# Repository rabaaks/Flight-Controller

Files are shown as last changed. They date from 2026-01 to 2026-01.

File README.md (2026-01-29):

# Custom Flight Controller

This is a custom flight controller and camera system that I designed to be used with Ardupilot for a drone or airplane. I made this to learn more about PCB design and also because I wanted a flight controller that I could use for my RC plane, so that I could setup autonomous flight and have better telemetry. I also wanted specific peripherals like the led strip and an OSD.

## Features

* STM32H743 Microcontroller
* BMP388 Pressure Sensor
* QMC5883 Magnetometeter
* ICM-42688 IMU
* OSD using MAX7456
* LED Strip
* 12 Motor Ouputs
* MicroSD Card
* 6 UARTs and 1 I2C

## Schematic

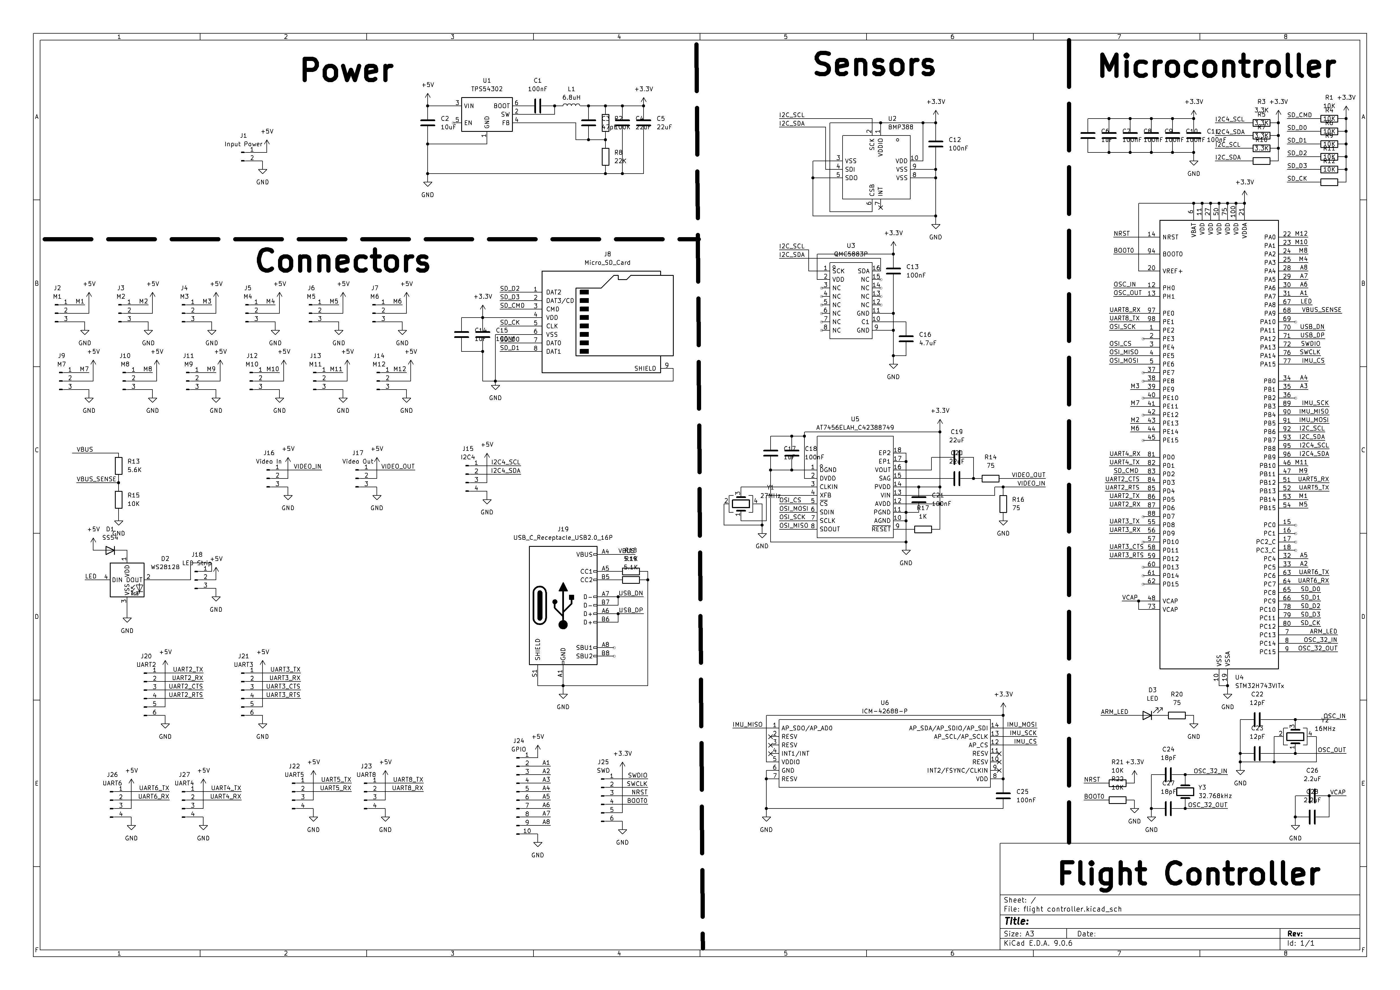
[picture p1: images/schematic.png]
Schematic


## PCB

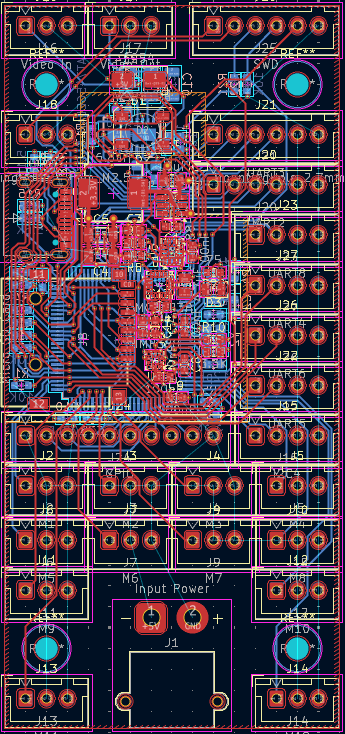
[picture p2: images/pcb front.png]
PCB Front

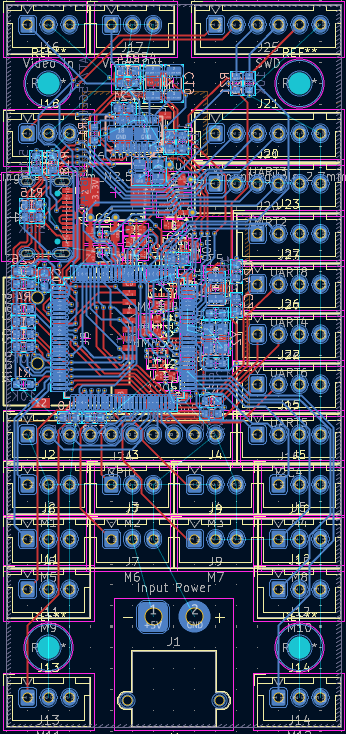
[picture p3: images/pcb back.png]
PCB Back


## Render

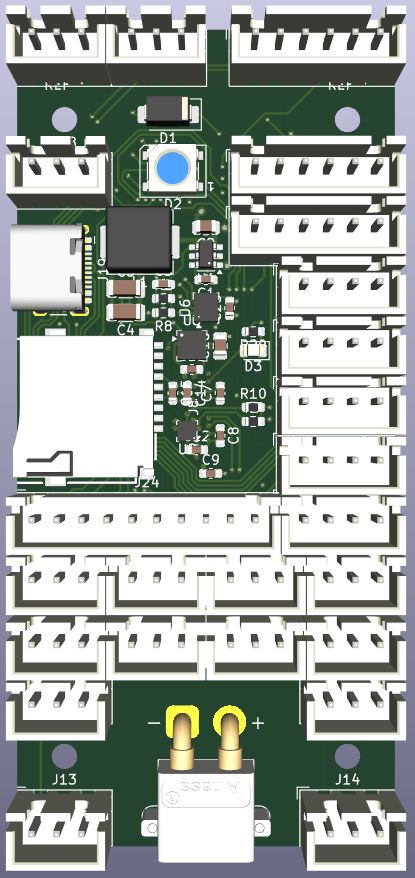
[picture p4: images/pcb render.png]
PCB Render


I also designed a basic camera system to be used with it, using RX5808 and TX5823S modules. It uses a camera and display from a car backup camera system which was a low cost option that uses analog video. The camera and display require 12v, while the radio modules require 5v, so some voltage conversion is necessary. This circuit will be assembled on 0.1" pitch perfboard.

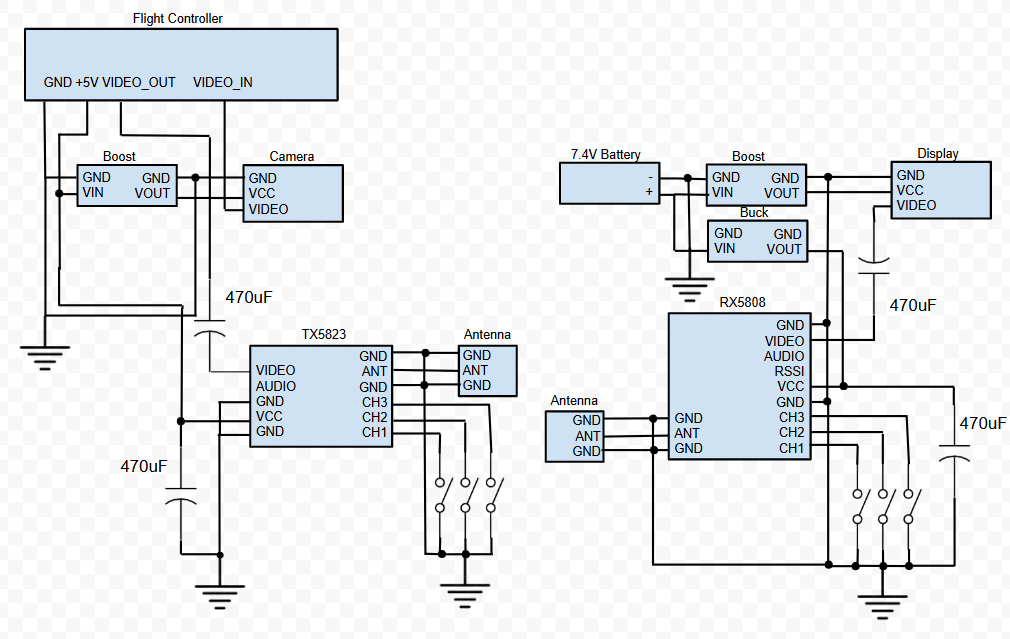
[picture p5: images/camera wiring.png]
Camera Wiring


## Bill of Materials

|Name |Quantity|Unit Price|Total Price|Link |FIELD6|Total Price|
|---|---|---|---|---|---|---|
|CL10B105KA8NNNC |50 |0.0062 |0.31 |https://www.lcsc.com/product-detail/C29936.html | |71.26 |
|CL10B104KB8NNNC |100 |0.0027 |0.27 |https://www.lcsc.com/product-detail/C1591.html | | |
|CL21B475KOFNNNE |10 |0.0191 |0.19 |https://www.lcsc.com/product-detail/C107365.html | | |
|CL21B106KOQNNNE |10 |0.0247 |0.25 |https://www.lcsc.com/product-detail/C95841.html | | |
|CL10C120JB8NNNC |100 |0.0047 |0.47 |https://www.lcsc.com/product-detail/C38523.html | | |
|CL10B225KP8NNNC |50 |0.0123 |0.62 |https://www.lcsc.com/product-detail/C100082.html | | |
|CL10C180JB8NNNC |100 |0.005 |0.5 |https://www.lcsc.com/product-detail/C1647.html | | |
|CL10C470JB8NNNC |100 |0.0031 |0.31 |https://www.lcsc.com/product-detail/C1671.html | | |
|CL31A226KOHNNNE |5 |0.0381 |0.19 |https://www.lcsc.com/product-detail/C90146.html | | |
|CL21B104KBCNNNC |50 |0.0065 |0.33 |https://www.lcsc.com/product-detail/C1711.html | | |
|SS54 |10 |0.0433 |0.43 |https://www.lcsc.com/product-detail/C22452.html | | |
|WS2812B-B/T |5 |0.0879 |0.44 |https://www.lcsc.com/product-detail/C2761795.html | | |
|NCD0805R1 |50 |0.0125 |0.63 |https://www.lcsc.com/product-detail/C84256.html | | |
|ZX-XH2.54-3PZZ |20 |0.01 |0.2 |https://www.lcsc.com/product-detail/C7429633.html | | |
|XT30PW-M30.G.Y |1 |0.2926 |0.29 |https://www.lcsc.com/product-detail/C431092.html | | |
|TYPE-C 16PIN 2MD(073) |20 |0.06 |1.2 |https://www.lcsc.com/product-detail/C2765186.html | | |
|ZX-XH2.54-6PZZ |20 |0.0198 |0.4 |https://www.lcsc.com/product-detail/C7429636.html | | |
|ZX-XH2.54-4PZZ |20 |0.0111 |0.22 |https://www.lcsc.com/product-detail/C7429634.html | | |
|ZX-XH2.54-10PZZ |10 |0.0434 |0.43 |https://www.lcsc.com/product-detail/C7429640.html | | |
|TF PUSH |10 |0.0568 |0.57 |https://www.lcsc.com/product-detail/C393941.html | | |
|APH0630T6R8M |10 |0.0633 |0.63 |https://www.lcsc.com/product-detail/C5349706.html | | |
|0603WAF5601T5E |100 |0.0012 |0.12 |https://www.lcsc.com/product-detail/C23189.html | | |
|0603WAF1001T5E |100 |0.0012 |0.12 |https://www.lcsc.com/product-detail/C21190.html | | |
|0603WAF5101T5E |100 |0.0012 |0.12 |https://www.lcsc.com/product-detail/C23186.html | | |
|0603WAF1003T5E |100 |0.0011 |0.11 |https://www.lcsc.com/product-detail/C25803.html | | |
|0603WAF750JT5E |100 |0.0013 |0.13 |https://www.lcsc.com/product-detail/C4275.html | | |
|0603WAF1002T5E |100 |0.0011 |0.11 |https://www.lcsc.com/product-detail/C25804.html | | |
|0603WAF3301T5E |100 |0.0012 |0.12 |https://www.lcsc.com/product-detail/C22978.html | | |
|0603WAF2202T5E |100 |0.0012 |0.12 |https://www.lcsc.com/product-detail/C31850.html | | |
|TPS54302DDCR |5 |0.1517 |0.76 |https://www.lcsc.com/product-detail/C311983.html | | |
|BMP388 |1 |2.7418 |2.74 |https://www.lcsc.com/product-detail/C779278.html | | |
|QMC5883P |1 |1.48 |1.48 |https://www.lcsc.com/product-detail/C2847467.html | | |
|STM32H743VIT6 |1 |7.1333 |7.13 |https://www.lcsc.com/product-detail/C114409.html | | |
|AT7456ELAH |1 |3.9151 |3.92 |https://www.lcsc.com/product-detail/C42388749.html  | | |
|ICM-42688-PC |1 |2.0211 |2.02 |https://www.lcsc.com/product-detail/C48586483.html  | | |
|X322527MSB4SI |10 |0.0718 |0.72 |https://www.lcsc.com/product-detail/C9008.html | | |
|X322516MLB4SI |10 |0.0678 |0.68 |https://www.lcsc.com/product-detail/C13738.html | | |
|X321532768KGD2SI |5 |0.2164 |1.08 |https://www.lcsc.com/product-detail/C620155.html | | |
|KM477M025F12RR0VH2FP0 |10 |0.0393 |0.39 |https://www.lcsc.com/product-detail/C43839.html | | |
|LED Strip 5m |1 |8.46 |8.46 |https://www.aliexpress.us/item/3256807796309465.html| | |
|MT3608 5pcs |1 |2.49 |2.49 |https://www.aliexpress.us/item/3256806175499915.html| | |
|MP1584 5pcs |1 |5.5 |5.5 |https://www.aliexpress.us/item/3256805119457659.html| | |
|RX5808 |1 |12.76 |12.76 |https://www.aliexpress.us/item/3256808812641407.html| | |
|TX5823S |1 |9.07 |9.07 |https://www.aliexpress.us/item/3256808812641407.html| | |
|VS-S4301 |1 |15.99 |15.99 |https://a.co/d/fmBpzXg | | |
|Bingfu Dual Band WiFi Antenna 2.4GHz 5/5.8GHz 3dBi SMA Male Antenna|1 |9.99 |9.99 |https://a.co/d/eEHf94O | | |
|4 Layer JLCPCB |1 |7 |7 |https://cart.jlcpcb.com/quote?stencilLayer=4 | | |

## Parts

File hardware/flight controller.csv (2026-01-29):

Id | Designator | Footprint | Quantity | Designation | Supplier and ref
39 | C14,C6,C17 | C_0603_1608Metric | 3 | 1uF | C29936
10 | C15 | C_0603_1608Metric | 1 | 100Nf | C1591
23 | C16 | C_0805_2012Metric | 1 | 4.7uF | C107365
24 | C2 | C_0805_2012Metric | 1 | 10uF | C95841
55 | C22,C23 | C_0603_1608Metric | 2 | 12pF | C38523
53 | C26,C28 | C_0603_1608Metric | 2 | 2.2uF | C100082
49 | C27,C24 | C_0603_1608Metric | 2 | 18pF | C1647
13 | C3 | C_0603_1608Metric | 1 | 47pF | C1671
12 | C4,C5,C20,C19 | C_1206_3216Metric | 4 | 22uF | C90146
3 | C9,C25,C1,C8,C7,C13,C12,C10,C11,C18,C21 | C_0603_1608Metric | 11 | 100nF | C1711
14 | D1 | D_SMA | 1 | SS54 | C22452
28 | D2 | LED_WS2812B_PLCC4_5.0x5.0mm_P3.2mm | 1 | WS2812B | C2761795
31 | D3 | LED_0805_2012Metric | 1 | LED | C84256
2 | J | JST_XH_B3B-XH-A_1x03_P2.50mm_Vertical | 15 | XH3 | C7429633
7 | J1 | AMASS_XT30PW-M_1x02_P2.50mm_Horizontal | 1 | Input Power | C431092
20 | J19 | USB_C_Receptacle_HCTL_HC-TYPE-C-16P-01A | 1 | USB_C_Receptacle_USB2.0_16P | C2765186
15 | J21 | JST_XH_B6B-XH-A_1x06_P2.50mm_Vertical | 3 | XH6 | C7429636
5 | J22 | JST_XH_B4B-XH-A_1x04_P2.50mm_Vertical | 5 | XH4 | C7429634
40 | J24 | JST_XH_B10B-XH-A_1x10_P2.50mm_Vertical | 1 | GPIO | C7429640
30 | J8 | TF-SMD_TF-PUSH | 1 | Micro_SD_Card | C393941
16 | L1 | L_APV_APH0630 | 1 | 6.8uH | C5349706
54 | R13 | R_0603_1608Metric | 1 | 5.6K | C23189
50 | R17 | R_0603_1608Metric | 1 | 1K | C21190
51 | R19,R18 | R_0603_1608Metric | 2 | 5.1K | C23186
1 | R2 | R_0603_1608Metric | 1 | 100K | C25803
44 | R20,R14,R16 | R_0603_1608Metric | 3 | 75 | C4275
47 | R6,R21,R4,R22,R1,R9,R12,R15,R11 | R_0603_1608Metric | 9 | 10K | C25804
26 | R7,R10,R3,R5 | R_0603_1608Metric | 4 | 3.3K | C22978
25 | R8 | R_0603_1608Metric | 1 | 22K | C31850
41 | U1 | SOT-23-6 | 1 | TPS54302 | C311983
35 | U2 | ST_HLGA-10_2x2mm_P0.5mm_LayoutBorder3x2y | 1 | BMP388 | C779278
37 | U3 | LGA-16_3x3mm_P0.5mm | 1 | QMC5883P | C2847467
58 | U4 | LQFP-100_14x14mm_P0.5mm | 1 | STM32H743VITx | C114409
52 | U5 | LGA-16_L6.8-W4.0-P0.65-TL-2EP | 1 | AT7456ELAH_C42388749 | C42388749
43 | U6 | LGA-14_3x2.5mm_P0.5mm_LayoutBorder3x4y | 1 | ICM-42688-P | C48586483
56 | Y1 | Crystal_SMD_3225-4Pin_3.2x2.5mm | 1 | 27MHz | C9008
57 | Y2 | Crystal_SMD_3225-4Pin_3.2x2.5mm | 1 | 16MHz | C13738
48 | Y3 | Crystal_SMD_3215-2Pin_3.2x1.5mm | 1 | 32.768kHz | C620155

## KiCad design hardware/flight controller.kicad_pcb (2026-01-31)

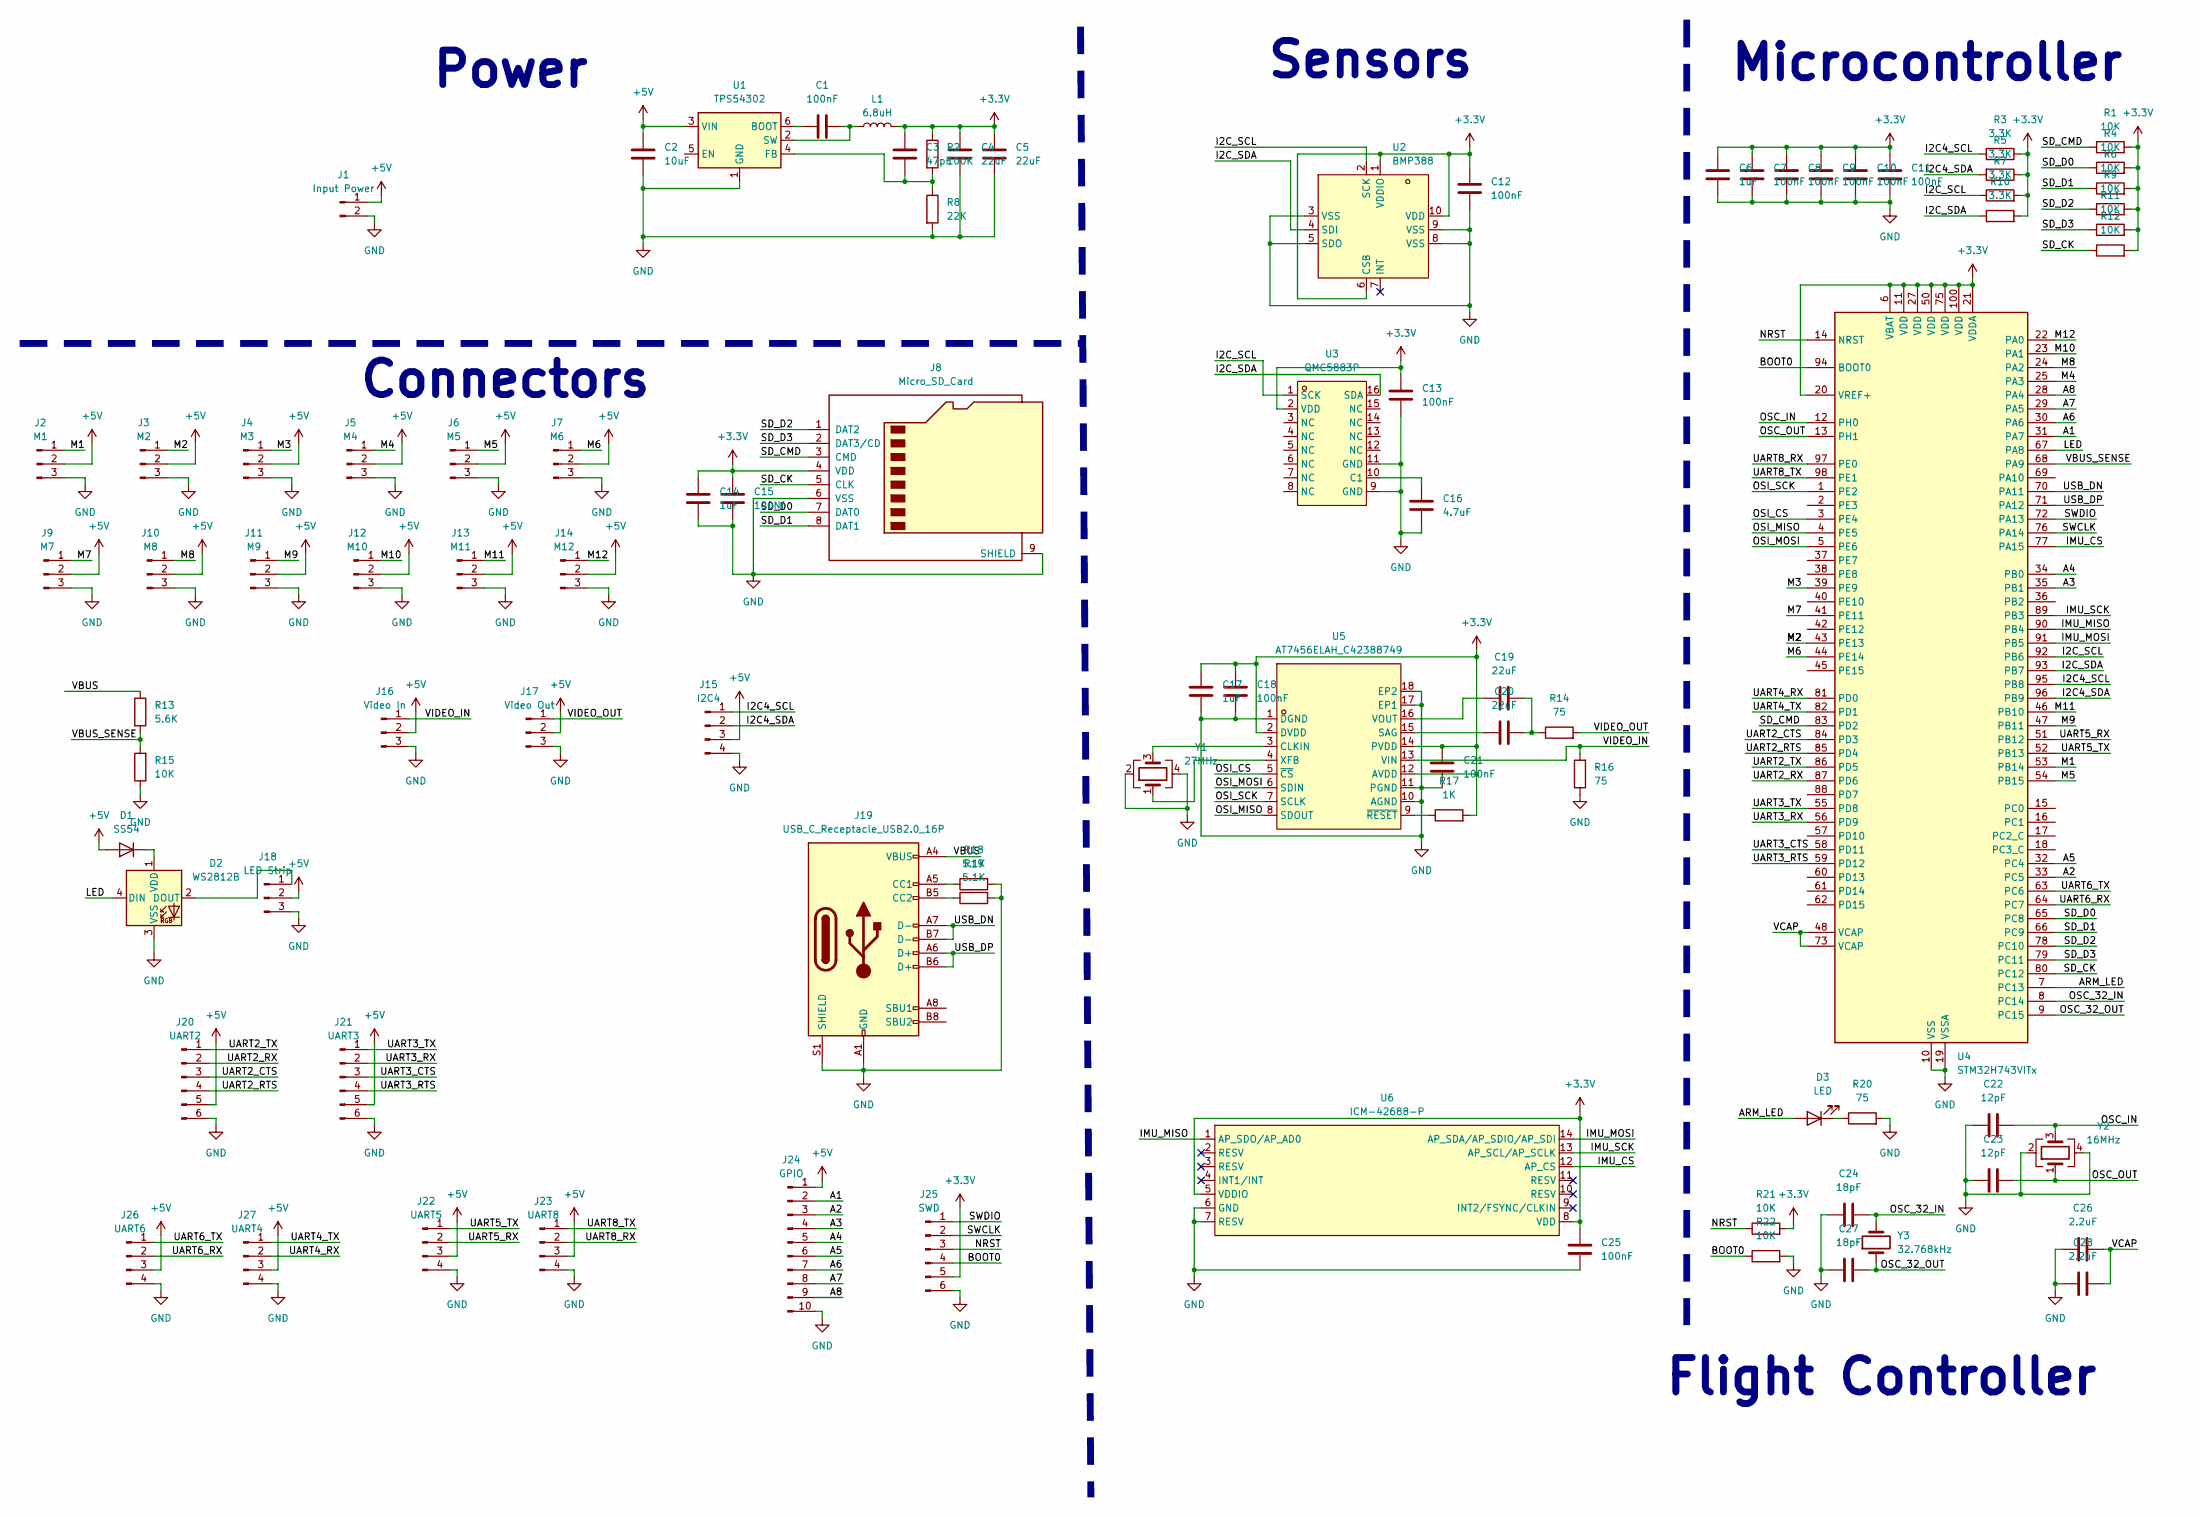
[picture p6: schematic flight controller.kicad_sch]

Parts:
C1, C7, C8, C9, C10, C11, C12, C13, C18, C21, C25: 100nF; C_0603_1608Metric
C2: 10uF; C_0805_2012Metric
C3: 47pF; C_0603_1608Metric
C4, C5, C19, C20: 22uF; C_1206_3216Metric
C6, C14, C17: 1uF; C_0603_1608Metric
C15: 100Nf; C_0603_1608Metric
C16: 4.7uF; C_0805_2012Metric
C22, C23: 12pF; C_0603_1608Metric
C24, C27: 18pF; C_0603_1608Metric
C26, C28: 2.2uF; C_0603_1608Metric
D1: SS54; D_SMA
D2: WS2812B; LED_WS2812B_PLCC4_5.0x5.0mm_P3.2mm
D3: LED; LED_0805_2012Metric
J1: Input Power; AMASS_XT30PW-M_1x02_P2.50mm_Horizontal
J2: M1; JST_XH_B3B-XH-A_1x03_P2.50mm_Vertical
J3: M2; JST_XH_B3B-XH-A_1x03_P2.50mm_Vertical
J4: M3; JST_XH_B3B-XH-A_1x03_P2.50mm_Vertical
J5: M4; JST_XH_B3B-XH-A_1x03_P2.50mm_Vertical
J6: M5; JST_XH_B3B-XH-A_1x03_P2.50mm_Vertical
J7: M6; JST_XH_B3B-XH-A_1x03_P2.50mm_Vertical
J8: Micro_SD_Card; TF-SMD_TF-PUSH
J9: M7; JST_XH_B3B-XH-A_1x03_P2.50mm_Vertical
J10: M8; JST_XH_B3B-XH-A_1x03_P2.50mm_Vertical
J11: M9; JST_XH_B3B-XH-A_1x03_P2.50mm_Vertical
J12: M10; JST_XH_B3B-XH-A_1x03_P2.50mm_Vertical
J13: M11; JST_XH_B3B-XH-A_1x03_P2.50mm_Vertical
J14: M12; JST_XH_B3B-XH-A_1x03_P2.50mm_Vertical
J15: I2C4; JST_XH_B4B-XH-A_1x04_P2.50mm_Vertical
J16: Video In; JST_XH_B3B-XH-A_1x03_P2.50mm_Vertical
J17: Video Out; JST_XH_B3B-XH-A_1x03_P2.50mm_Vertical
J18: LED Strip; JST_XH_B3B-XH-A_1x03_P2.50mm_Vertical
J19: USB_C_Receptacle_USB2.0_16P; USB_C_Receptacle_HCTL_HC-TYPE-C-16P-01A
J20: UART2; JST_XH_B6B-XH-A_1x06_P2.50mm_Vertical
J21: UART3; JST_XH_B6B-XH-A_1x06_P2.50mm_Vertical
J22: UART5; JST_XH_B4B-XH-A_1x04_P2.50mm_Vertical
J23: UART8; JST_XH_B4B-XH-A_1x04_P2.50mm_Vertical
J24: GPIO; JST_XH_B10B-XH-A_1x10_P2.50mm_Vertical
J25: SWD; JST_XH_B6B-XH-A_1x06_P2.50mm_Vertical
J26: UART6; JST_XH_B4B-XH-A_1x04_P2.50mm_Vertical
J27: UART4; JST_XH_B4B-XH-A_1x04_P2.50mm_Vertical
L1: 6.8uH; L_APV_APH0630
R1, R4, R6, R9, R11, R12, R15, R21, R22: 10K; R_0603_1608Metric
R2: 100K; R_0603_1608Metric
R3, R5, R7, R10: 3.3K; R_0603_1608Metric
R8: 22K; R_0603_1608Metric
R13: 5.6K; R_0603_1608Metric
R14, R16, R20: 75; R_0603_1608Metric
R17: 1K; R_0603_1608Metric
R18, R19: 5.1K; R_0603_1608Metric
U1: TPS54302; SOT-23-6
U2: BMP388; ST_HLGA-10_2x2mm_P0.5mm_LayoutBorder3x2y; LCSC Part C779278
U3: QMC5883P; LGA-16_3x3mm_P0.5mm; LCSC Part C2847467
U4: STM32H743VITx; LQFP-100_14x14mm_P0.5mm
U5: AT7456ELAH_C42388749; LGA-16_L6.8-W4.0-P0.65-TL-2EP; LCSC Part C42388749
U6: ICM-42688-P; LGA-14_3x2.5mm_P0.5mm_LayoutBorder3x4y; LCSC Part C1850418
Y1: 27MHz; Crystal_SMD_3225-4Pin_3.2x2.5mm
Y2: 16MHz; Crystal_SMD_3225-4Pin_3.2x2.5mm
Y3: 32.768kHz; Crystal_SMD_3215-2Pin_3.2x1.5mm

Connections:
+3.3V: C3.1, C4.2, C5.1, C6.2, C7.1, C8.2, C9.1, C10.2, C11.2, C12.2, C13.1, C14.2, C15.2, C17.1, C18.1, C21.1, C25.2, J8.4 (VDD), J25.5, L1.2, R1.2, R2.1, R3.1, R4.2, R5.1, R6.2, R7.2, R9.2, R10.2, R11.2, R12.2, R17.2, R21.2, U2.1 (VDDIO), U2.6 (CSB), U2.10 (VDD), U3.2 (VDD), U4.6 (VBAT), U4.11 (VDD), U4.20 (VREF+), U4.21 (VDDA), U4.27 (VDD), U4.50 (VDD), U4.75 (VDD), U4.100 (VDD), U5.2 (DVDD), U5.12 (AVDD), U5.14 (PVDD), U6.5 (VDDIO), U6.8 (VDD)
+5V: C2.1, D1.2 (A), J1.1, J2.2, J3.2, J4.2, J5.2, J6.2, J7.2, J9.2, J10.2, J11.2, J12.2, J13.2, J14.2, J15.3, J16.2, J17.2, J18.2, J20.5, J21.5, J22.3, J23.3, J24.1, J26.3, J27.3, U1.3 (VIN)
/A1: J24.2, U4.31 (PA7)
/A2: J24.3, U4.33 (PC5)
/A3: J24.4, U4.35 (PB1)
/A4: J24.5, U4.34 (PB0)
/A5: J24.6, U4.32 (PC4)
/A6: J24.7, U4.30 (PA6)
/A7: J24.8, U4.29 (PA5)
/A8: J24.9, U4.28 (PA4)
/ARM_LED: D3.2 (A), U4.7 (PC13)
/BOOT0: J25.4, R22.1, U4.94 (BOOT0)
/I2C4_SCL: J15.1, R3.2, U4.95 (PB8)
/I2C4_SDA: J15.2, R5.2, U4.96 (PB9)
/I2C_SCL: R7.1, U2.2 (SCK), U3.1 (SCK), U4.92 (PB6)
/I2C_SDA: R10.1, U2.4 (SDI), U3.16 (SDA), U4.93 (PB7)
/IMU_CS: U4.77 (PA15), U6.12 (AP_CS)
/IMU_MISO: U4.90 (PB4), U6.1 (AP_SDO/AP_AD0)
/IMU_MOSI: U4.91 (PB5), U6.14 (AP_SDA/AP_SDIO/AP_SDI)
/IMU_SCK: U4.89 (PB3), U6.13 (AP_SCL/AP_SCLK)
/LED: D2.4 (DIN), U4.67 (PA8)
/M1: J2.1, U4.53 (PB14)
/M2: J3.1, U4.43 (PE13)
/M3: J4.1, U4.39 (PE9)
/M4: J5.1, U4.25 (PA3)
/M5: J6.1, U4.54 (PB15)
/M6: J7.1, U4.44 (PE14)
/M7: J9.1, U4.41 (PE11)
/M8: J10.1, U4.24 (PA2)
/M9: J11.1, U4.47 (PB11)
/M10: J12.1, U4.23 (PA1)
/M11: J13.1, U4.46 (PB10)
/M12: J14.1, U4.22 (PA0)
/NRST: J25.3, R21.1, U4.14 (NRST)
/OSC_32_IN: C24.1, U4.8 (PC14), Y3.2
/OSC_32_OUT: C27.2, U4.9 (PC15), Y3.1
/OSC_IN: C22.1, U4.12 (PH0), Y2.3
/OSC_OUT: C23.2, U4.13 (PH1), Y2.1
/OSI_CS: U4.3 (PE4), U5.5 (~CS)
/OSI_MISO: U4.4 (PE5), U5.8 (SDOUT)
/OSI_MOSI: U4.5 (PE6), U5.6 (SDIN)
/OSI_SCK: U4.1 (PE2), U5.7 (SCLK)
/SD_CK: J8.5 (CLK), R12.1, U4.80 (PC12)
/SD_CMD: J8.3 (CMD), R1.1, U4.83 (PD2)
/SD_D0: J8.7 (DAT0), R4.1, U4.65 (PC8)
/SD_D1: J8.8 (DAT1), R6.1, U4.66 (PC9)
/SD_D2: J8.1 (DAT2), R9.1, U4.78 (PC10)
/SD_D3: J8.2 (DAT3/CD), R11.1, U4.79 (PC11)
/SWCLK: J25.2, U4.76 (PA14)
/SWDIO: J25.1, U4.72 (PA13)
/UART2_CTS: J20.3, U4.84 (PD3)
/UART2_RTS: J20.4, U4.85 (PD4)
/UART2_RX: J20.2, U4.87 (PD6)
/UART2_TX: J20.1, U4.86 (PD5)
/UART3_CTS: J21.3, U4.58 (PD11)
/UART3_RTS: J21.4, U4.59 (PD12)
/UART3_RX: J21.2, U4.56 (PD9)
/UART3_TX: J21.1, U4.55 (PD8)
/UART4_RX: J27.2, U4.81 (PD0)
/UART4_TX: J27.1, U4.82 (PD1)
/UART5_RX: J22.2, U4.51 (PB12)
/UART5_TX: J22.1, U4.52 (PB13)
/UART6_RX: J26.2, U4.64 (PC7)
/UART6_TX: J26.1, U4.63 (PC6)
/UART8_RX: J23.2, U4.97 (PE0)
/UART8_TX: J23.1, U4.98 (PE1)
/USB_DN: J19.A7 (D-), J19.B7 (D-), U4.70 (PA11)
/USB_DP: J19.A6 (D+), J19.B6 (D+), U4.71 (PA12)
/VBUS: J19.A4 (VBUS), J19.A9 (VBUS), J19.B4 (VBUS), J19.B9 (VBUS), R13.1
/VBUS_SENSE: R13.2, R15.2, U4.68 (PA9)
/VCAP: C26.1, C28.1, U4.48 (VCAP), U4.73 (VCAP)
/VIDEO_IN: J16.1, R16.2, U5.13 (VIN)
/VIDEO_OUT: J17.1, R14.2
GND: C2.2, C4.1, C5.2, C6.1, C7.2, C8.1, C9.2, C10.1, C11.1, C12.1, C13.2, C14.1, C15.1, C16.2, C17.2, C18.2, C21.2, C22.2, C23.1, C24.2, C25.1, C26.2, C27.1, C28.2, D2.3 (VSS), J1.2, J2.3, J3.3, J4.3, J5.3, J6.3, J7.3, J8.6 (VSS), J8.9 (SHIELD), J9.3, J10.3, J11.3, J12.3, J13.3, J14.3, J15.4, J16.3, J17.3, J18.3, J19.A1 (GND), J19.A12 (GND), J19.B1 (GND), J19.B12 (GND), J19.S1 (SHIELD), J20.6, J21.6, J22.4, J23.4, J24.10, J25.6, J26.4, J27.4, R8.2, R15.1, R16.1, R18.2, R19.2, R20.2, R22.2, U1.1 (GND), U2.3 (VSS), U2.5 (SDO), U2.8 (VSS), U2.9 (VSS), U3.9 (GND), U3.11 (GND), U4.10 (VSS), U4.19 (VSSA), U4.26 (VSS), U4.49 (VSS), U4.74 (VSS), U4.99 (VSS), U5.1 (DGND), U5.10 (AGND), U5.11 (PGND), U5.17 (EP1), U5.18 (EP2), U6.6 (GND), U6.7 (RESV), Y1.2, Y1.4, Y2.2, Y2.4
unnamed: C19.2, C20.2, R14.1
unnamed: D1.1 (K), D2.1 (VDD)
unnamed: D2.2 (DOUT), J18.1
unnamed: D3.1 (K), R20.1
unnamed: J19.A5 (CC1), R18.1
unnamed: J19.B5 (CC2), R19.1
unnamed: C1.2, U1.6 (BOOT)
unnamed: C3.2, R2.2, R8.1, U1.4 (FB)
unnamed: C1.1, L1.1, U1.2 (SW)
unnamed: C16.1, U3.10 (C1)
unnamed: U5.3 (CLKIN), Y1.3
unnamed: C20.1, U5.15 (SAG)
unnamed: C19.1, U5.16 (VOUT)
unnamed: U5.4 (XFB), Y1.1
unnamed: R17.1, U5.9 (~RESET)

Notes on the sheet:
Microcontroller
Connectors
Sensors
Flight Controller
Power

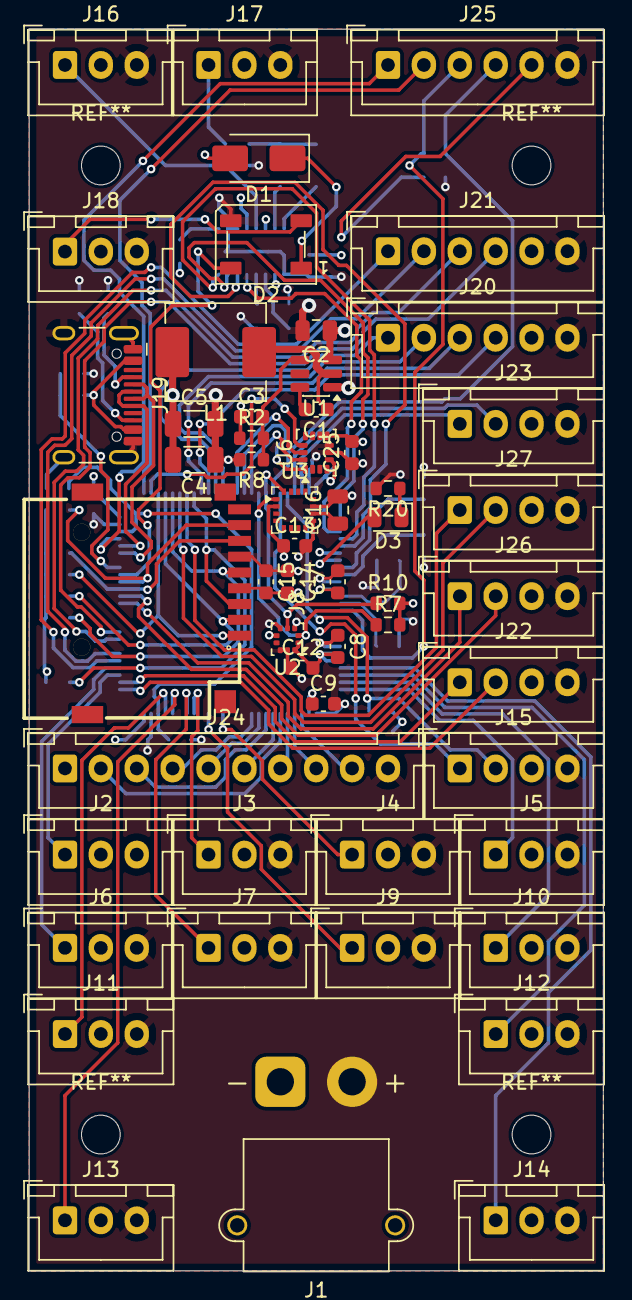
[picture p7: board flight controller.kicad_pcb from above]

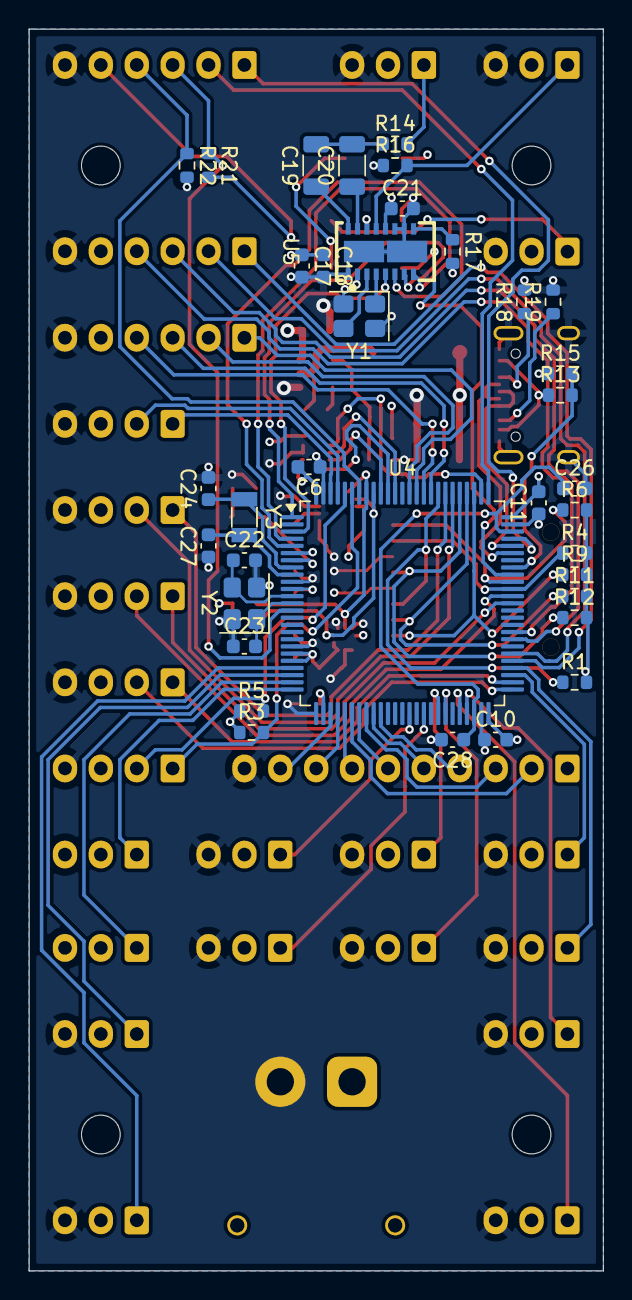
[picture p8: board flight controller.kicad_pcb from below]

Board: 4 copper layers, 40.0 x 86.5 mm, 90 parts (36 on the bottom side), 89 nets.

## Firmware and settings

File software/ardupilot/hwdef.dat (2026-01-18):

MCU STM32H743xx
OSCILLATOR_HZ 16000000
FLASH_SIZE_KB 2048
BOOTLOADER_RESERVE_KB 128

BOARD CUSTOM_H743
APJ_BOARD_ID 1234

PA11 USB_DM
PA12 USB_DP
PA9  VBUS

PA13 SWDIO
PA14 SWCLK

PE3 LED_ARM OUTPUT LOW
PA8 LED_NEOPIXEL OUTPUT

PA0 UART2_TX
PA3 UART2_RX

PD8 UART3_TX
PD9 UART3_RX

PD0 UART4_TX
PD1 UART4_RX

PB12 UART5_TX
PB13 UART5_RX

PE7 UART7_TX
PE10 UART7_RX

PE0 UART8_TX
PE1 UART8_RX

PB3 SPI1_SCK
PB4 SPI1_MISO
PB5 SPI1_MOSI
PA15 SPI1_CS_IMU

PE2 SPI4_SCK
PE5 SPI4_MISO
PE6 SPI4_MOSI
PE4 SPI4_CS_OSD

SPIDEV icm42688 spi1 CS=SPI1_CS_IMU MODE=3
OSD MAX7456 SPI4 CS=SPI4_CS_OSD

PB6 I2C1_SCL
PB7 I2C1_SDA

PB8 I2C4_SCL
PB9 I2C4_SDA

BARO BMP388 I2C:1
COMPASS LIS3MDL I2C:1

PC8  SDMMC1_D0
PC9  SDMMC1_D1
PC10 SDMMC1_D2
PC11 SDMMC1_D3
PC12 SDMMC1_CK
PD2  SDMMC1_CMD

PE13 TIM1_CH3
PE14 TIM1_CH4

PD12 TIM4_CH1
PD13 TIM4_CH2
PD14 TIM4_CH3
PD15 TIM4_CH4

PB10 TIM2_CH3
PB11 TIM2_CH4

PB14 TIM12_CH1
PB15 TIM12_CH2

PC6 TIM8_CH1
PC7 TIM8_CH2

PA1 GPIO
PA2 GPIO
PA3 GPIO
PA4 GPIO
PA5 GPIO
PA6 GPIO
PA7 GPIO
PB0 GPIO
PB1 GPIO
PC4 GPIO
PC5 GPIO

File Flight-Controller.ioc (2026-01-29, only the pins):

Mcu.UserName=STM32H743VITx
PA0.Signal=S_TIM5_CH1
PA1.Signal=S_TIM5_CH2
PA11.Signal=USB_OTG_FS_DM
PA12.Signal=USB_OTG_FS_DP
PA2.Signal=S_TIM5_CH3
PA3.Signal=S_TIM5_CH4
PA4.Signal=ADCx_INP18
PA5.Signal=ADCx_INP19
PA6.Signal=ADCx_INP3
PA7.Signal=ADCx_INP7
PA9.Signal=USB_OTG_FS_VBUS
PB0.Signal=ADCx_INP9
PB1.Signal=ADCx_INP5
PB10.Signal=S_TIM2_CH3
PB11.Signal=S_TIM2_CH4
PB12.Signal=UART5_RX
PB13.Signal=UART5_TX
PB14.Signal=S_TIM12_CH1
PB15.Signal=S_TIM12_CH2
PB5.Signal=SPI1_MOSI
PB6.Signal=I2C1_SCL
PB7.Signal=I2C1_SDA
PB8.Signal=I2C4_SCL
PB9.Signal=I2C4_SDA
PC10.Signal=SDMMC1_D2
PC11.Signal=SDMMC1_D3
PC12.Signal=SDMMC1_CK
PC13.Signal=GPIO_Output
PC4.Signal=ADCx_INP4
PC5.Signal=ADCx_INP8
PC6.Signal=USART6_TX
PC7.Signal=USART6_RX
PC8.Signal=SDMMC1_D0
PC9.Signal=SDMMC1_D1
PD0.Signal=UART4_RX
PD1.Signal=UART4_TX
PD11.Signal=USART3_CTS
PD12.Signal=USART3_RTS
PD2.Signal=SDMMC1_CMD
PD3.Signal=USART2_CTS
PD4.Signal=USART2_RTS
PD5.Signal=USART2_TX
PD6.Signal=USART2_RX
PD8.Signal=USART3_TX
PD9.Signal=USART3_RX
PE0.Signal=UART8_RX
PE1.Signal=UART8_TX
PE11.Signal=S_TIM1_CH2
PE13.Signal=S_TIM1_CH3
PE14.Signal=S_TIM1_CH4
PE2.Signal=SPI4_SCK
PE4.Signal=SPI4_NSS
PE5.Signal=SPI4_MISO
PE6.Signal=SPI4_MOSI
PE9.Signal=S_TIM1_CH1

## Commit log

2026-01-18 finished pcb
    [flight controller.kicad_pcb, flight controller.kicad_sch]
2026-01-18 add images and readme
    [bom.csv, designators.csv, flight controller.kicad_pcb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]
2026-01-19 finished bom
    [bom.csv, flight controller.csv, flight controller.kicad_pcb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]
2026-01-19 remove production folder
    [designators.csv, positions.csv]
2026-01-19 changed the regulator to a buck converter
    [flight controller.kicad_pcb]
2026-01-19 added antenna stuff
    [bom.csv]
2026-01-19 update bom
2026-01-22 smd crystal
    [flight controller.kicad_pcb, flight controller.kicad_sch]
2026-01-23 some routing
    [flight controller.kicad_pcb, flight controller.kicad_sch]
2026-01-23 more routing
    [flight controller.kicad_pcb]
2026-01-29 finish v2
    [bom.csv, flight controller.csv, flight controller.kicad_pcb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]
2026-01-31 add gerber files
    [flight controller-B_Cu.gbl, flight controller-B_Mask.gbs, flight controller-B_Paste.gbp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]
2026-01-31 update bom, fix some clearance issue
    [bom.csv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]
